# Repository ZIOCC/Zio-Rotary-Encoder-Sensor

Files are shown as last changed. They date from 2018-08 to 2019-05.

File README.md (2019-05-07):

# Zio Rotary Encoder Sensor
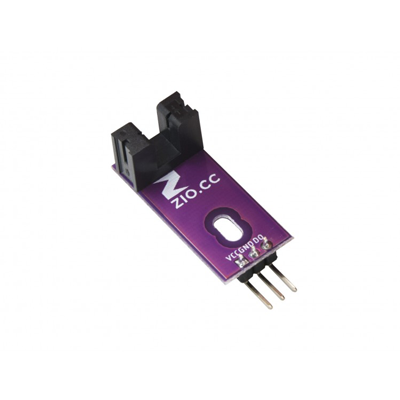
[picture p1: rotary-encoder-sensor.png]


> This product can be available for purchase [here](https://www.smart-prototyping.com/Zio-Rotary-Encoder-Sensor).

#### Description

This is a U-Shaped infrared sensor that can be used to detect the rotational speed of a motor mounted on a robot. This reading can be used to adjust the motor speed if it is too fast or too slow, and to calculate the robot’s real-world travel speed. Using a pair of these sensors, we can also measure the robot’s rotation, enabling navigation based on dead-reckoning methods.

#### Specification

* U-Shaped Sensor Gap: 5mm
* Output Signal Explaination: when the IR beam is unobstructed (not blocked by the encoder disc) it outputs a logic-LOW level(0); when blocked it outputs HIGH Level(1).
* IR Signal Trigger: SN74LVC1G14 Single Schmitt-Trigger Inverter
* Dimension: 32x 14mm
* Weight: 1.9g

#### Links

* [Eagle file](https://github.com/ZIOCC/Zio-Rotary-Encoder-Sensor/)
* [How IR Sensor Works](https://www.digikey.com/en/articles/techzone/2012/feb/using-infrared-technology-for-sensing)
* [SN74LVC1G14 Datasheet](http://www.ti.com/lit/ds/symlink/sn74lvc1g14.pdf)

> ###### About Zio
> Zio is a new line of open sourced, compact, and grid layout boards, fully integrated for Arduino and Qwiic ecosystem. Designed ideally for wearables, robotics, small-space limitations or other on the go projects. Check out other awesome Zio products [here](https://www.smart-prototyping.com/Zio).

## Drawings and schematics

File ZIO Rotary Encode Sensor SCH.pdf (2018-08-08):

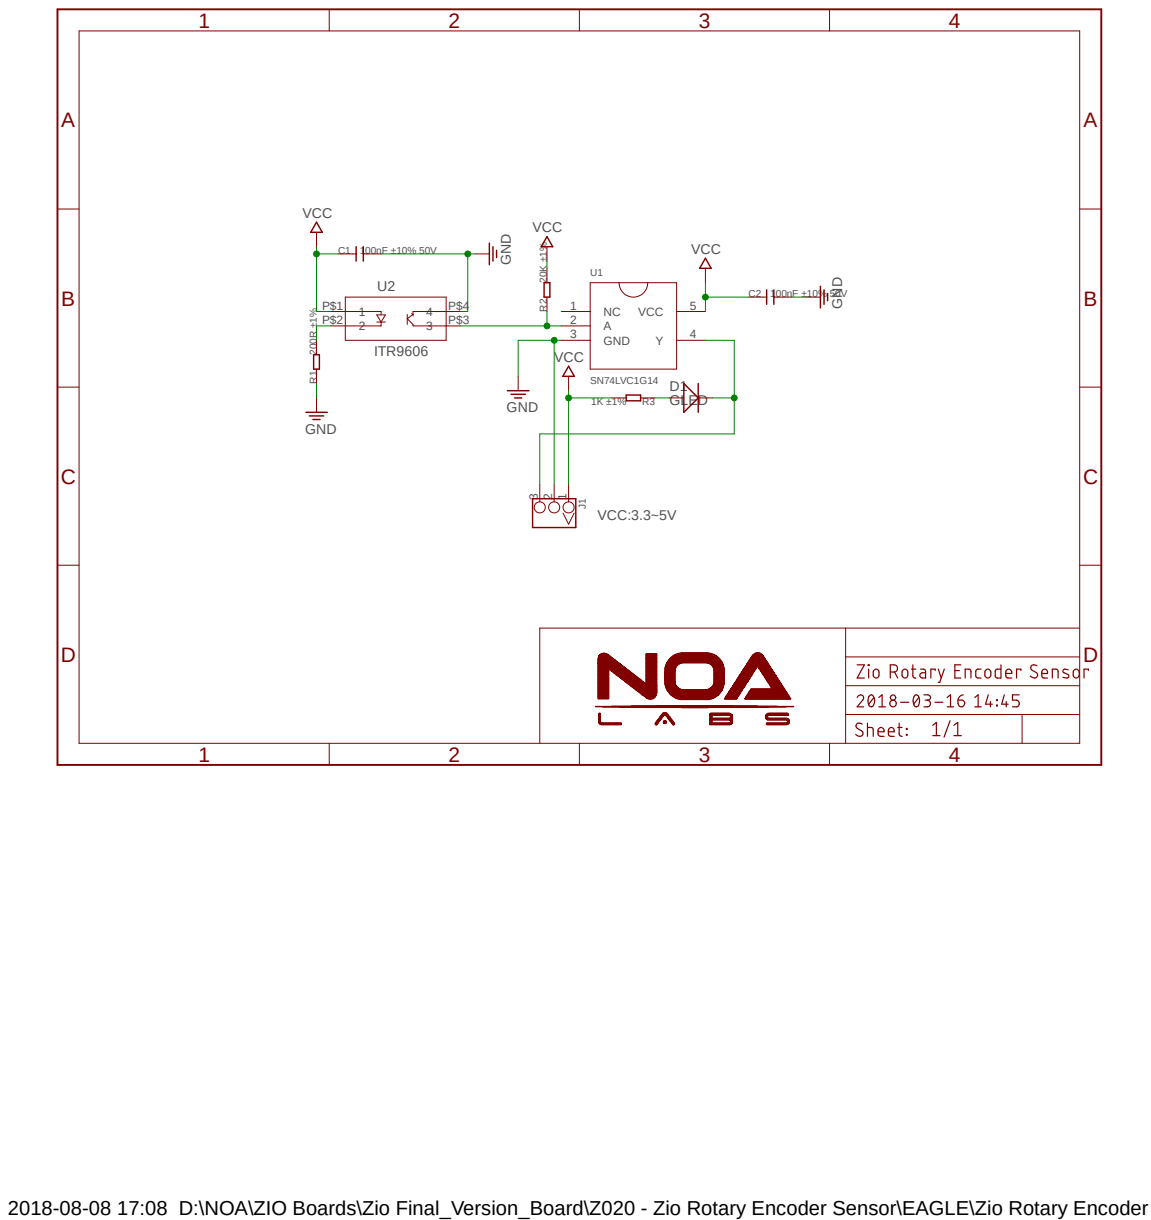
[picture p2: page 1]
SN74LVC1G14 ²⁰⁰R ±1%; ITR9606; 100nF ±10% 50V VCC; VCC; GND; GND GND; GLED; VCCJ13; GND 3; VCC:3.3~5V

2018-08-08 17:08 D:\NOA\ZIO Boards\Zio Final_Version_Board\Z020 - Zio Rotary Encoder Sensor\EAGLE\Zio Rotary Encoder Sensor.sch (Sheet: 1/1)

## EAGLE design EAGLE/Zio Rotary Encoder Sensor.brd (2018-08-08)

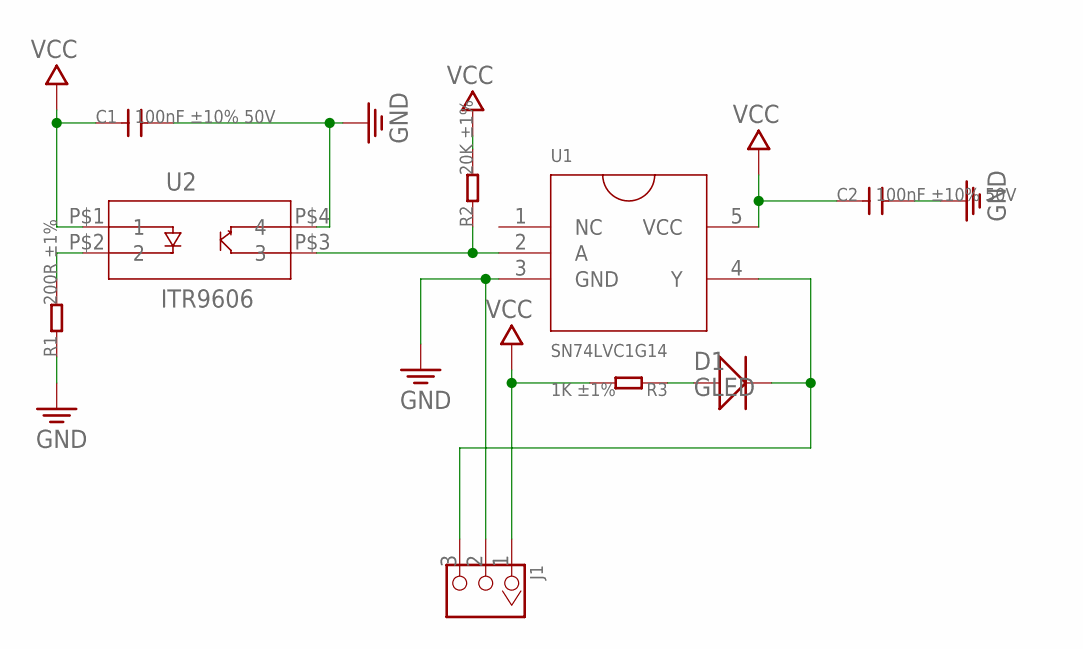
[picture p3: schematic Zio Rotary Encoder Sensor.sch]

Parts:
C1, C2: 100nF ±10% 50V; 0603
D1: GLED; SOD523
J1: HEADER-3P-2.54; 3P-2.54
R1: 200R ±1%; 0603
R2: 20K ±1%; 0603
R3: 1K ±1%; 0603
U1: SN74LVC1G14; SOT23-5
U2: ITR9606

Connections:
GND: C1.2, C2.2, J1.2, R1.1, U1.3 (GND), U2.P$4 (4)
unnamed: R1.2, U2.P$2 (2)
unnamed: R2.1, U1.2 (A), U2.P$3 (3)
unnamed: D1.+, R3.1
unnamed: D1.-, J1.3, U1.4 (Y)
VCC: C1.1, C2.1, J1.1, R2.2, R3.2, U1.5 (VCC), U2.P$1 (1)

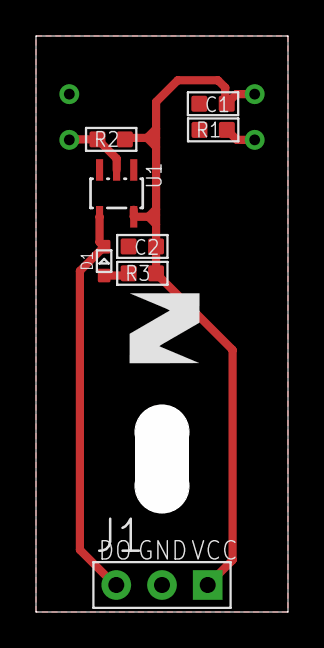
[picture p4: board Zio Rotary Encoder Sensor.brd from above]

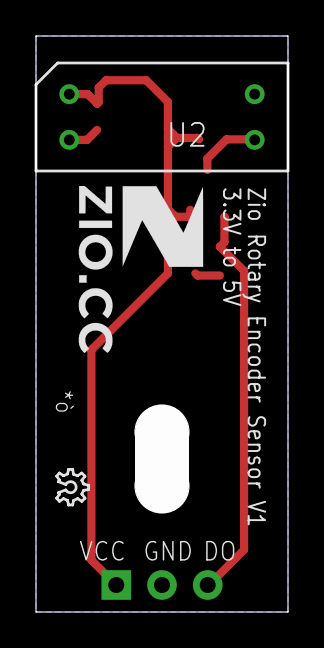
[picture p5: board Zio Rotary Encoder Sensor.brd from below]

Board: 2 copper layers, 14.0 x 32.0 mm, 12 parts (3 on the bottom side), 6 nets.

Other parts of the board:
U$5: 6MM
U$6: 7MM
U$7: OSHW_6X70_NOTEXT
